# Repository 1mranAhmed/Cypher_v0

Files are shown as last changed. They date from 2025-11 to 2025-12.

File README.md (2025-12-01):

This is Cypher. An autonomous All Terrain Rover, designed to provide help and during Disasters, and decrease the respnse delay. 

Cypher pic

Features : 
  1. Autonomous Navigation
  2. All Terrain
  3. Surveillance and Neutralization
  4. Fire Extingushing
  5. Med-Kit Deployment
  6. Swappable Robotic Arm

Details:

   1. Autonomous Navigation:
   We panned to achieve autonomous Navigation using the SLAM Directory, with ROS2 Humble. The sensors that we were planning on using were 2 motor mounted magnetic encoders of 1300 CPR, an IMU, and a TFmini LiDAR. We were able to implement autonomous navigation on a predictable path. The predictable path was 1 metre forward, 1 metre backwards, 1 metre left and 1 metre right. The processing for this Odometry was done on the Arduino Due. The Arduino Due was chosen for its powerful processor (ARM Cortex M3) and large number of Interrupt capable pins.
    
   2. All Terrain:
  We used the Rocker-Bogie Mechanism developed by NASA to achieve the All Terrain capability. The main body was made using a sheet of Mild Steel 3mm thickness. It was laser cut to ensure precision. Though, the whole Rocker-Bogie Mechanism, which was implemented on the Mars Rover wasnt implemented. A basic Version of it was used instead. The basic Design was done on solidWorks. The image is attached Below:  
  Cypher all terrain mech

   3. Surveillance and Neutralization:
      This was done using Python and OpenCV library. A model was trained to detect specific objects. The Python Script detected the object and calculated the error from the centre of the detected object to the center of the frame and sent this data to the Microcontroller via Serial Communication. The MicroController contolled the servos the track the detected object and neutralize the detected object.

   4. Fire Extinguisher: 
      The same Model was trained to detect Fires and actuate a Relay. The Fire Extinguisher system consisted of a Air Cannister, Solenoid Switch and Relay. Upon Detection of Fire, the Relay is Actuated and the supressant in the Air Cannister is released.   
  5. Med-Kit Deployment:
      The same Model was trained to detect an injured person. When detected, a servo is actuated to open and throw out a Med-kit for the injured Person.
    6. Swappable Robotic Arm: 
      This Feature is swappable with the neutralizing mechanism, to help assist civilians during disaster situations. 

The main idea was to integrate all of these Features using ROS2, but due to our current technical expretise, we werent able to achieve it. It is a Future goal for now, one we hope to achieve.

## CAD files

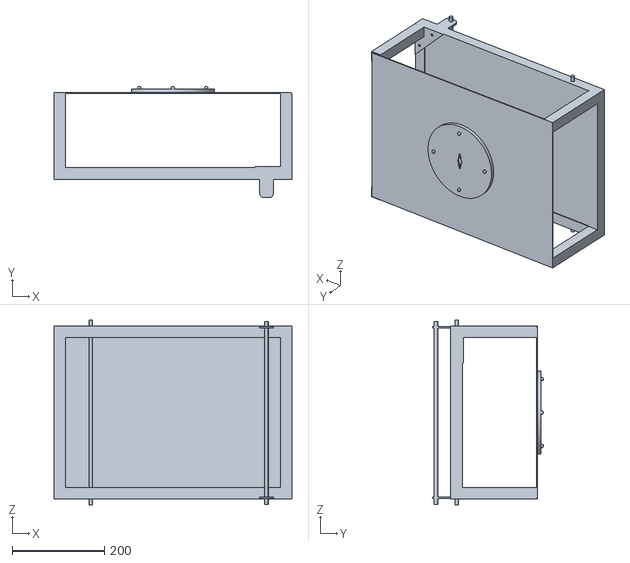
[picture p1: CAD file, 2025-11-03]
src/cypher_description/meshes/base_link.STL
515.4 x 241.4 x 400.0

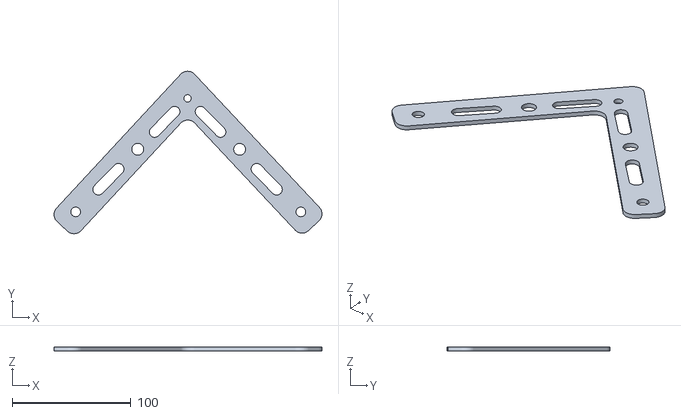
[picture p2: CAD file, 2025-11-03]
src/cypher_description/meshes/rocker_link.STL
225.3 x 136.7 x 3.00

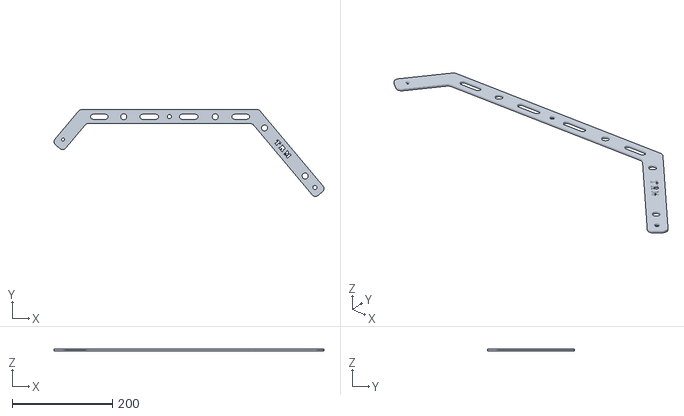
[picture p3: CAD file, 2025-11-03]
src/cypher_description/meshes/bogie_link.STL
537.8 x 173.1 x 3.00

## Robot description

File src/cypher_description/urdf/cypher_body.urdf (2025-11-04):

<?xml version="1.0"?>
<robot name="box">

  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

  <link name="base_link">
    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
  </link>
  
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
  <link name = "left_bogie_horizontal_strip">
    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
  </link>

 <joint name = "left_Bogie_to_Base_chassis_joint" type = "revolute">
    <parent link = "base_link"/>
    <child link = "left_bogie_horizontal_strip"/>
    <origin xyz = "0.245 -0.175 0.2233" rpy = "0 0 0"/>
    <axis xyz="0 1 0"/>
    <limit lower="-1.5708" upper="1.5708" effort="50" velocity="1.0"/>
  </joint>


  <link name = "left_bogie_rear_wheel_strip">
    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
  </link>

  <joint name = "left_rear_wheel_strip_to_horizontal_strip" type = "fixed">
    <parent link = "left_bogie_horizontal_strip"/>
    <child link = "left_bogie_rear_wheel_strip"/>
    <origin xyz = "0.195 -0.175 0.2233" rpy = "0 0 0"/>
    <axis xyz="0 0 0"/>
  </joint>

  <link name = "left_bogie_to_rocker_strip">
  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
  </link>

  <joint name = "left_bogie_to_rocker_joint" type = "fixed">
    <parent link = "left_bogie_horizontal_strip"/>
    <child link = "left_bogie_to_rocker_strip"/>
    <origin xyz = " -0.195 -0.175 0.15" rpy = "0 0 0"/>
    <axis xyz = "0 0 0"/>
  </joint>

  <link name = "left_rocker_frontwheel_strip">
  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
  </link>

  <link name = "left_rocker_midwheel_strip">
  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
  </link>

  <joint name = "left_rocker_joint" type = "fixed">
    <parent link = "left_rocker_frontwheel_strip"/>
    <child link = "left_rocker_midwheel_strip"/>
    <origin xyz = " -0.195 -0.175 0.138" rpy = "0 0 0"/>
    <axis xyz = "0 0 0"/>
  </joint>

  <joint name = "left_rocker_joint_to_bogie" type = "revolute">
    <parent link = "left_bogie_horizontal_strip"/>
    <child link = "left_rocker_frontwheel_strip"/>
    <origin xyz = " -0.195 -0.175 0.138" rpy = "0 0 0"/>
    <axis xyz = "0 0 0"/>
    <limit lower="-1.5708" upper="1.5708" effort="50" velocity="1.0"/>
  </joint>

  <link name="left_front_wheel">
    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
  </link>

  <joint name = "left_front_wheel_joint" type = "continuous">
    <parent link = "left_rocker_frontwheel_strip"/>
    <child link = "left_front_wheel"/>
    <origin xyz = " -0.3 -0.175 0.075" rpy = "0 0 0"/>
    <axis xyz = "0 1 0"/>
  </joint>

  <link name="left_mid_wheel">
    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
  </link>

  <joint name = "left_front_mid_joint" type = "continuous">
    <parent link = "left_rocker_midwheel_strip"/>
    <child link = "left_mid_wheel"/>
    <origin xyz = " -0.1 -0.175 0.075" rpy = "0 0 0"/>
    <axis xyz = "0 1 0"/>
  </joint>
 
  <link name="left_rear_wheel">
    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
  </link>

  <joint name = "left_front_rear_joint" type = "continuous">
    <parent link = "left_bogie_rear_wheel_strip"/>
    <child link = "left_rear_wheel"/>
    <origin xyz = " 0.25 -0.175 0.075" rpy = "0 0 0"/>
    <axis xyz = "0 1 0"/>
  </joint>
 
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
  <link name = "right_bogie_horizontal_strip">
    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
  </link>

 <joint name = "right_Bogie_to_Base_chassis_joint" type = "revolute">
    <parent link = "base_link"/>
    <child link = "right_bogie_horizontal_strip"/>
    <origin xyz = "0.245 0.175 0.2233" rpy = "0 0 0"/>
    <axis xyz="0 1 0"/>
    <limit lower="-1.5708" upper="1.5708" effort="50" velocity="1.0"/>
  </joint>


  <link name = "right_bogie_rear_wheel_strip">
    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
  </link>

  <joint name = "rear_wheel_strip_to_horizontal_strip" type = "fixed">
    <parent link = "right_bogie_horizontal_strip"/>
    <child link = "right_bogie_rear_wheel_strip"/>
    <origin xyz = "0.195 0.175 0.2233" rpy = "0 0 0"/>
    <axis xyz="0 0 0"/>
  </joint>

  <link name = "right_bogie_to_rocker_strip">
  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
  </link>

  <joint name = "right_bogie_to_rocker_joint" type = "fixed">
    <parent link = "right_bogie_horizontal_strip"/>
    <child link = "right_bogie_to_rocker_strip"/>
    <origin xyz = " -0.195 0.175 0.15" rpy = "0 0 0"/>
    <axis xyz = "0 0 0"/>
  </joint>

  <link name = "right_rocker_frontwheel_strip">
  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
  </link>

  <link name = "right_rocker_midwheel_strip">
  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
  </link>

  <joint name = "right_rocker_joint" type = "fixed">
    <parent link = "right_rocker_frontwheel_strip"/>
    <child link = "right_rocker_midwheel_strip"/>
    <origin xyz = " -0.195 0.175 0.138" rpy = "0 0 0"/>
    <axis xyz = "0 0 0"/>
  </joint>

  <joint name = "right_rocker_joint_to_bogie" type = "revolute">
    <parent link = "right_bogie_horizontal_strip"/>
    <child link = "right_rocker_frontwheel_strip"/>
    <origin xyz = " -0.195 0.175 0.138" rpy = "0 0 0"/>
    <axis xyz = "0 0 0"/>
    <limit lower="-1.5708" upper="1.5708" effort="50" velocity="1.0"/>
  </joint>

  <link name="right_front_wheel">
    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
  </link>

  <joint name = "right_front_wheel_joint" type = "continuous">
    <parent link = "right_rocker_frontwheel_strip"/>
    <child link = "right_front_wheel"/>
    <origin xyz = " -0.3 0.175 0.075" rpy = "0 0 0"/>
    <axis xyz = "0 1 0"/>
  </joint>

  <link name="right_mid_wheel">
    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
  </link>

  <joint name = "right_front_mid_joint" type = "continuous">
    <parent link = "right_rocker_midwheel_strip"/>
    <child link = "right_mid_wheel"/>
    <origin xyz = " -0.1 0.175 0.075" rpy = "0 0 0"/>
    <axis xyz = "0 1 0"/>
  </joint>
 
  <link name="right_rear_wheel">
    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
  </link>

  <joint name = "right_front_rear_joint" type = "continuous">
    <parent link = "right_bogie_rear_wheel_strip"/>
    <child link = "right_rear_wheel"/>
    <origin xyz = " 0.25 0.175 0.075" rpy = "0 0 0"/>
    <axis xyz = "0 1 0"/>
  </joint>
</robot>

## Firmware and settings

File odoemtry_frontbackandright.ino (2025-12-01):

// ===========================================================
// ⚙️ ODOMETRY-BASED 1M FORWARD + 90° RIGHT TURN
// ===========================================================

int FL_IN1 = 23, FL_IN2 = 22, FL_PWM = 2;
int FR_IN1 = 24, FR_IN2 = 25, FR_PWM = 3;
int BL_IN1 = 26, BL_IN2 = 27, BL_PWM = 4;
int BR_IN1 = 29, BR_IN2 = 28, BR_PWM = 5;
int speedVal = 80;        // Normal driving speed
int turnSpeed = 130;      // 🔹 Higher torque speed for turning

#define ENCODER_L_A 34
#define ENCODER_L_B 35
#define ENCODER_R_A 32
#define ENCODER_R_B 33

volatile long leftCount = 0, rightCount = 0;
volatile int lastEncodedLeft = 0, lastEncodedRight = 0;

const float WHEEL_DIAMETER_M = 0.150;
const float WHEEL_CIRCUMFERENCE_M = 3.14159265 * WHEEL_DIAMETER_M;
const float CPR = 1300.0;
const float WHEELBASE_M = 0.50;
const float CALIBRATION_FACTOR = 1.00;
const float METERS_PER_TICK = (WHEEL_CIRCUMFERENCE_M / CPR) * CALIBRATION_FACTOR;

float x = 0, y = 0, theta = 0;

// ================== ENCODERS ==================
void readEncoderLeft() {
  int MSB = digitalRead(ENCODER_L_A);
  int LSB = digitalRead(ENCODER_L_B);
  int encoded = (MSB << 1) | LSB;
  int sum = (lastEncodedLeft << 2) | encoded;
  switch (sum) {
    case 0b0001: case 0b0111: case 0b1110: case 0b1000: leftCount++; break;
    case 0b0010: case 0b0100: case 0b1101: case 0b1011: leftCount--; break;
  }
  lastEncodedLeft = encoded;
}
void readEncoderRight() {
  int MSB = digitalRead(ENCODER_R_A);
  int LSB = digitalRead(ENCODER_R_B);
  int encoded = (MSB << 1) | LSB;
  int sum = (lastEncodedRight << 2) | encoded;
  switch (sum) {
    case 0b0001: case 0b0111: case 0b1110: case 0b1000: rightCount++; break;
    case 0b0010: case 0b0100: case 0b1101: case 0b1011: rightCount--; break;
  }
  lastEncodedRight = encoded;
}

// ================== MOTOR CONTROL ==================
void moveForward(int s) {
  digitalWrite(FL_IN1, HIGH); digitalWrite(FL_IN2, LOW);
  digitalWrite(FR_IN1, HIGH); digitalWrite(FR_IN2, LOW);
  digitalWrite(BL_IN1, HIGH); digitalWrite(BL_IN2, LOW);
  digitalWrite(BR_IN1, HIGH); digitalWrite(BR_IN2, LOW);
  analogWrite(FL_PWM, s); analogWrite(FR_PWM, s);
  analogWrite(BL_PWM, s); analogWrite(BR_PWM, s);
}
void moveBackward(int s) {
  digitalWrite(FL_IN1, LOW); digitalWrite(FL_IN2, HIGH);
  digitalWrite(FR_IN1, LOW); digitalWrite(FR_IN2, HIGH);
  digitalWrite(BL_IN1, LOW); digitalWrite(BL_IN2, HIGH);
  digitalWrite(BR_IN1, LOW); digitalWrite(BR_IN2, HIGH);
  analogWrite(FL_PWM, s); analogWrite(FR_PWM, s);
  analogWrite(BL_PWM, s); analogWrite(BR_PWM, s);
}
void rotateRight(int s) {
  digitalWrite(FL_IN1, HIGH); digitalWrite(FL_IN2, LOW);
  digitalWrite(BL_IN1, HIGH); digitalWrite(BL_IN2, LOW);
  digitalWrite(FR_IN1, LOW);  digitalWrite(FR_IN2, HIGH);
  digitalWrite(BR_IN1, LOW);  digitalWrite(BR_IN2, HIGH);
  analogWrite(FL_PWM, s); analogWrite(FR_PWM, s);
  analogWrite(BL_PWM, s); analogWrite(BR_PWM, s);
}
void rotateLeft(int s) {
  digitalWrite(FL_IN1, LOW);  digitalWrite(FL_IN2, HIGH);
  digitalWrite(BL_IN1, LOW);  digitalWrite(BL_IN2, HIGH);
  digitalWrite(FR_IN1, HIGH); digitalWrite(FR_IN2, LOW);
  digitalWrite(BR_IN1, HIGH); digitalWrite(BR_IN2, LOW);
  analogWrite(FL_PWM, s); analogWrite(FR_PWM, s);
  analogWrite(BL_PWM, s); analogWrite(BR_PWM, s);
}
void stopMotors() {
  analogWrite(FL_PWM, 0); analogWrite(FR_PWM, 0);
  analogWrite(BL_PWM, 0); analogWrite(BR_PWM, 0);
  digitalWrite(FL_IN1, HIGH); digitalWrite(FL_IN2, HIGH);
  digitalWrite(FR_IN1, HIGH); digitalWrite(FR_IN2, HIGH);
  digitalWrite(BL_IN1, HIGH); digitalWrite(BL_IN2, HIGH);
  digitalWrite(BR_IN1, HIGH); digitalWrite(BR_IN2, HIGH);
}

// ================== UPDATE ODOMETRY ==================
void updateOdometry() {
  static long lastLeft = 0, lastRight = 0;
  noInterrupts();
  long leftNow = leftCount, rightNow = rightCount;
  interrupts();

  long deltaL = leftNow - lastLeft;
  long deltaR = rightNow - lastRight;

  float distL = -deltaL * METERS_PER_TICK;
  float distR =  deltaR * METERS_PER_TICK;

  float deltaD = (distR + distL) / 2.0;
  float deltaTheta = (distR - distL) / WHEELBASE_M;
  float theta_mid = theta + deltaTheta / 2.0;

  x += deltaD * cos(theta_mid);
  y += deltaD * sin(theta_mid);
  theta += deltaTheta;

  if (theta > 3.14159265)  theta -= 2 * 3.14159265;
  if (theta < -3.14159265) theta += 2 * 3.14159265;

  lastLeft = leftNow; lastRight = rightNow;
}

// ================== MOVE + TURN ==================
void moveForwardBy(float distance_m) {
  float startX = x, startY = y;
  moveForward(speedVal);

  while (true) {
    updateOdometry();
    float dx = x - startX;
    float dy = y - startY;
    float traveled = sqrt(dx * dx + dy * dy);
    Serial.print("FORWARD | Traveled: "); Serial.print(traveled, 3);
    Serial.print(" m | X: "); Serial.print(x, 3);
    Serial.print(" | Y: "); Serial.print(y, 3);
    Serial.print(" | Θ: "); Serial.println(theta * 180.0 / 3.14159, 2);

    if (traveled >= distance_m) break;
    delay(100);
  }
  stopMotors();
  delay(500);
}

// 🔹 Stronger rotation with short torque kick
void rotateRightBy90() {
  float startTheta = theta;
  float targetTheta = startTheta - (3.14159265 / 2.0);
  if (targetTheta < -3.14159265) targetTheta += 2 * 3.14159265;

  Serial.println("Turning Right 90°...");
  
  // 🔹 Kickstart turn
  rotateRight(180);
  delay(300);
  
  rotateRight(turnSpeed);
  while (true) {
    updateOdometry();
    Serial.print("TURNING | Θ: "); Serial.println(theta * 180.0 / 3.14159, 2);
    if (fabs(theta - targetTheta) < 0.08) break;  // 🔹 Wider tolerance
    delay(100);
  }
  stopMotors();
  delay(500);
}

void rotateLeftBy90() {
  float startTheta = theta;
  float targetTheta = startTheta + (3.14159265 / 2.0);
  if (targetTheta > 3.14159265) targetTheta -= 2 * 3.14159265;

  Serial.println("Turning Left 90°...");
  rotateLeft(180);
  delay(300);
  
  rotateLeft(turnSpeed);
  while (true) {
    updateOdometry();
    Serial.print("TURNING | Θ: "); Serial.println(theta * 180.0 / 3.14159, 2);
    if (fabs(theta - targetTheta) < 0.08) break;
    delay(100);
  }
  stopMotors();
  delay(500);
}

// ================== MAIN ==================
void setup() {
  Serial.begin(115200);
  pinMode(FL_IN1, OUTPUT); pinMode(FL_IN2, OUTPUT); pinMode(FL_PWM, OUTPUT);
  pinMode(FR_IN1, OUTPUT); pinMode(FR_IN2, OUTPUT); pinMode(FR_PWM, OUTPUT);
  pinMode(BL_IN1, OUTPUT); pinMode(BL_IN2, OUTPUT); pinMode(BL_PWM, OUTPUT);
  pinMode(BR_IN1, OUTPUT); pinMode(BR_IN2, OUTPUT); pinMode(BR_PWM, OUTPUT);

  pinMode(ENCODER_L_A, INPUT_PULLUP);
  pinMode(ENCODER_L_B, INPUT_PULLUP);
  pinMode(ENCODER_R_A, INPUT_PULLUP);
  pinMode(ENCODER_R_B, INPUT_PULLUP);

  lastEncodedLeft = (digitalRead(ENCODER_L_A) << 1) | digitalRead(ENCODER_L_B);
  lastEncodedRight = (digitalRead(ENCODER_R_A) << 1) | digitalRead(ENCODER_R_B);

  attachInterrupt(digitalPinToInterrupt(ENCODER_L_A), readEncoderLeft, CHANGE);
  attachInterrupt(digitalPinToInterrupt(ENCODER_L_B), readEncoderLeft, CHANGE);
  attachInterrupt(digitalPinToInterrupt(ENCODER_R_A), readEncoderRight, CHANGE);
  attachInterrupt(digitalPinToInterrupt(ENCODER_R_B), readEncoderRight, CHANGE);

  delay(1000);
  Serial.println("\n=== Starting Sequence ===");
}

void loop() {
  moveForwardBy(1.0);
  moveBackward(80
    
  );
  delay(1200); // Move roughly 1m back (simple timing)
  stopMotors();

  rotateRightBy90();
  rotateLeftBy90();

  stopMotors();
  Serial.println("\n=== Sequence Complete ===");
  while (1);
}

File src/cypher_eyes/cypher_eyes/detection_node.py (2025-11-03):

import rclpy
from rclpy.node import Node
from ultralytics import YOLO
import cv2
from geometry_msgs.msg import Point

class ObjectDetectionNode(Node):
    def __init__(self):
        super().__init__('object_detection_node')
        self.publisher_ = self.create_publisher(Point, '/detected_object', 10)

        # Load YOLO model (path inside your package)
        self.model = YOLO("/home/imran/ros2_ws/src/my_robot_controller/my_robot_controller/best.pt")

        # Open webcam
        self.cap = cv2.VideoCapture(0)
        if not self.cap.isOpened():
            self.get_logger().error("Failed to open camera")
            raise RuntimeError("Camera not available")

        # Timer for callback (~20 Hz)
        self.timer = self.create_timer(0.05, self.detect_callback)

        # Calibration constant for distance estimation
        self.CALIBRATION_K = 10.0

        # Frame size (for center calculation)
        self.frame_width = int(self.cap.get(cv2.CAP_PROP_FRAME_WIDTH))
        self.frame_height = int(self.cap.get(cv2.CAP_PROP_FRAME_HEIGHT))
        self.frame_center = (self.frame_width // 2, self.frame_height // 2)

        self.get_logger().info("Object detection node initialized.")

    def estimate_distance(self, bbox_height):
        """Estimate distance based on bounding box height."""
        if bbox_height > 0:
            return self.CALIBRATION_K / bbox_height
        else:
            return None

    def detect_callback(self):
        ret, frame = self.cap.read()
        if not ret:
            self.get_logger().warn("Camera frame not received.")
            return

        results = self.model(frame, verbose=False)

        for r in results:
            boxes = r.boxes
            if len(boxes) == 0:
                continue

            # Pick the most confident detection only
            best_box = max(boxes, key=lambda b: float(b.conf[0]))
            x1, y1, x2, y2 = map(int, best_box.xyxy[0])
            conf = float(best_box.conf[0])

            bbox_height = y2 - y1
            distance_m = self.estimate_distance(bbox_height)
            if not distance_m:
                continue

            # Compute object center
            cx = (x1 + x2) // 2
            cy = (y1 + y2) // 2

            # Publish as a geometry_msgs/Point
            msg = Point()
            msg.x = float(cx)
            msg.y = float(cy)
            msg.z = float(distance_m)
            self.publisher_.publish(msg)

            # Visualization (optional)
            cv2.rectangle(frame, (x1, y1), (x2, y2), (0, 255, 0), 2)
            cv2.circle(frame, (cx, cy), 5, (0, 0, 255), -1)
            cv2.putText(frame, f"{distance_m:.2f}m ({conf:.2f})",
                        (x1, y1 - 10), cv2.FONT_HERSHEY_SIMPLEX,
                        0.6, (0, 255, 0), 2)
            cv2.imshow("YOLO Detection", frame)
            cv2.waitKey(1)

    def destroy_node(self):
        """Ensure clean resource release."""
        self.cap.release()
        cv2.destroyAllWindows()
        super().destroy_node()


def main(args=None):
    rclpy.init(args=args)
    node = ObjectDetectionNode()
    try:
        rclpy.spin(node)
    except KeyboardInterrupt:
        node.get_logger().info("Shutting down node...")
    finally:
        node.destroy_node()
        rclpy.shutdown()


if __name__ == '__main__':
    main()

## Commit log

2025-11-03 Re-added cypher_description as normal package
    [base_link.STL, bogie_link.STL, cypher_body.urdf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]
2025-11-04 Changed the URDF according to Rviz. Physics might be wonky
    [cypher_body.urdf]
2025-11-04 URDF Changed. no Physics yet
    [cypher_body.urdf]
2025-12-01 Add files via upload
    Added the Odometry File for Front, back and right movement
